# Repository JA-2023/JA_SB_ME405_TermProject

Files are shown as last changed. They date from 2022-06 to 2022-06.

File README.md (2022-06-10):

# Mechanical Design

For our robot we decided to go with a pantograph design which is a four arm system that is in the shape of a pentagram. This system is controlled by two stepper motors and connected at the end effector point. For the mechanical design we wanted to base it around the ability to be easily assembled and changed with little effort. To do this, we made a simple base that would hold the paper, electronics, and a raised platform on a hinge that the motors would sit on. For the arms, we wanted something light yet sturdy so we cut 4 arm linkages out of acrylic. For the joints of these arms, we wanted something to allow for fluid motion so we used standard bolts with nyloc nuts to allow for a snug but moveable connection. For the pen holder at the end of the arms, we used a brass sleeve bearing, which has a natural lubrication and a rubber grommet to make for a secure connection. To implement this design a 3D model was made using solidworks. From this 3D model made .DXF files and used to laser cut the arms from an acrylic sheet. The base was made from simple materials consisting of wood, screws, and metal hinges. For the half degree of degree of freedom a solenoid was connected to the motor platform and lifted via the hinges. There were some issues with this design which will be expanded upon in the problems/issues section.



                                           Figure 1:  3D model of pantograph robot

# Functionality

The Functionality of the Pantograph is intended to draw basic shapes, with two arms conjoined together and moving in a synchronized motion where at the intersection of the two arms, the pen is attached and drawing along the motion, if the pen in the instance is not suppose to draw anything , or go to the proper destination with no drawing, a solenoid is used (see Mechanical Design for more detail) to raise the platform , lifting the pen off the platform (see Figure 2 for a visual representation on how the Pantograph is suppose to work).  

 

                                          Figure 2: Pantograph Drawing a Square

# Kinematics

Forward Kinematics 

To calculate the Kinematics of the Pantograph, the design of the Pantograph is considered. In Figure 3 given four arms , four lengths are given : L1, L2, L3 , L4 and four angles : 𝛳<sub>1</sub>, 𝛳<sub>2</sub>, 𝛳<sub>3</sub>, 𝛳<sub>4</sub>.  The kinematics of the pantograph can be calculated. In Figure 3, C<sub>n</sub> and S<sub>n</sub> represent cos(𝛳<sub>n</sub>) and sin(𝛳<sub>n</sub>) respectively. Since we have two arms, the final destination, (x,y) is made up of two coordinates : (x<sub>1</sub>,y<sub>1</sub>), (x<sub>2</sub>, y<sub>2</sub>), with trigonometry , (x,y ) is calculated ( See Figure 3),    



                                          Figure 3: Kinematic model of system and Calculations

Inverse Kinematics 

The Inverse Kinematics is necessary , since in the Pantograph, it is taking the x-y coordinates as 

inputs , since the user wants to input coordinates and the robot needs to calculate the necessary angles to get the desired position. In order to calculate the inverse kinematics of the equation.The four kinematic equations are set up in a matrix as  f(𝛉) :

          

                                              Figure 4 - x, 𝛉, and  f(𝛉) set  as matrices.

Once set, the Jacobian matrix was found 



                                                   Figure 5 - Jacobian Matrix of f(𝛉)

Hence the coordinates , x is now a function of 𝛉 and since the Jacobian matrix is found, then it is possible to find the velocity kinematics  of the system  .



                                             Figure 6 - Velocity Kinematics of the Pantograph

Due to the level of complexity of the kinematics ,the velocity kinematics is utilized to help find the  Newton-Raphson algorithm,  a simple root-finding algorithm to iteratively solve the inverse kinematics, until the forward kinematics lands on a desired value for x. To do this first  g() needs to be solved for (see Figure 7), once solved,  g is solved for then (Figure 8).



                                              Figure 7 - Finding g()

                              

                                              Figure 8 - Finding g 

This new equation ( Figure 7) is selected so when g() is 0.  You can find the roots with the Newton Rhapson (Figure 9). The Newton-Raphson algorithm is a single-step iterative procedure for finding the roots of differential equations. In vector form and applied to this problem, The Newton-Raphson step would follow:

 

                                              Figure 9 - Newton-Raphson algorithm

where  n is the step number or number of iterations through the algorithm. The algorithm must stop when the value of g() is sufficiently close to zero by a threshold.

# Software Implementation and Design

## Driver Design



                                             Figure 10: Class diagram of the motor driver class

For the driver design the focus was on basic functionality that could be expanded upon if desired. The init class sets up the TMC2208 and TMC 4210 motor drivers to allow the motor to move. It sets up the necessary pins and SPI signals on the nucleo board as well as the clock, velocity, acceleration, movement mode, and so on. The set velocity, set acceleration, and acceleration calculations methods are used in the init class to set up the TMC drivers. The send and receive methods will take the datagram to be sent and then pull the chip select signal for a specific peripheral low and send the datagram through SPI. The set position method will take the target position datagram as a parameter. The target position is then passed into the function and bit masked,  so that the correct value is sent to the X position register of the TMC 4210. The read position method will read the data in the X actual register of the TMC 4210 and return the data read.

## Implementation of Kinematics

To solve the kinematics of the system for many different end effector positions a script was made that implements the kinematics described above. This script takes position values and puts them through three methods to output the desired motor angles. These methods are g which finds the difference between f(θ) and the destination, dg_dtheta which finds the jacobian, and NewtonRaphson which implements the iterative method described earlier. The Newton-Raphson function is passed a lambda function that allows the function to run continuously as if it was given theta values. Additionally a helper function, matmul, which multiplies a 4x1 matrix and a 4x4 matrix is used since there are limitations to micropython.

## Parsing Vector Images/interpolation

To allow the system to draw the desired shapes a vector drawing software was used and then that image was saved in a hpgl format. This format gives x and y coordinates along with a set of commands for controlling machines which are separated by semicolons (;). These commands include ones such as pen up (PU), select pen (SP), and pen down (PD). Pen down/up are the two main commands that were used for this system. These hpgl files were read as one large string and then were split at each semicolon to separate each command. Once that was done, each command was separated into a list which consisted of the command, a list of x positions, and a list of y positions.

Since our system is not perfect and the robot does not move smoothly from one point to the next, each point requires interpolation which is the process of adding more points between points to make smoother lines. Once all of the values are parsed they go through an interpolation script which adds the extra points and scales/off sets the positional values for this specific system. After that is done, all of the points go through the Newton-Raphson process to be changed to motor angles and written to a text file stored in the system flash to reduce the memory usage of the system. 

## Task Organization

To make this system work multiple elements had to work in tandem to make the robot work effectively. To do this a system called cotask was used which works as a way of scheduling tasks to make them seem to work simultaneously. This system works with 5 different tasks. The first and main task is read command. The read command task will read commands/motor angle values from a precompile text file and determine from the text which task it should execute next. If the command is pen up (PU), then the system will put a flag high indicating that the pen up task should begin. In the pen up task the system will turn on a solenoid, which in turn lifts the platform that the motors are on and then it will raise the read flag, so that the next command can be read. 

If the value read is pen down (PD), then it will raise a pen down flag and go to the pen down task. In this task, it will turn off the solenoid and then raise the flag to read another command. If the next command is a number then it will raise a flag to start the move arms task, and will then read the values for motor one and motor two and put them into shares. In the move arms task it will take the motor values from the shares and send the position to the motor driver to move the arms to the specified position. After the position is set the system will go to the update LCD task which will take those motor positions and send them to an LCD to give user feedback. Once this is done the read flag will be set high and the system will continue.



                                          Figure 11 - state diagram of task management

# Issues/Improvements to make

## Mechanical

Arm to motor connection:

One of the main issues encountered was the connection of the acrylic arms to the motor shaft. A good connection was not able to be made which resulted in the arm sometimes slipping and not moving correctly. To reduce this slipping, a wedge was used to make for a tighter connection. This was helpful but it is not intended to be a permanent solution. Due to this poor connection and the weight of the arms/hardware connected, the arms would sag down making them harder to move in a smooth and controlled fashion.

To fix this problem it would have been best to instead implement a gear reduction system and have the arms mesh with a gear to make a more secure connection. Also the material of the arms at the joints and end effector should be changed to a lighter material to reduce the drag. On top of this it would be better to implement a clamping mechanism to hold the pen instead of a wedging solution to allow for more fine tuning and flexibility.

Pen choice:

For this system we used a felt tip pen which would often bleed out onto the paper which did not make clean lines. The felt pen allowed for easy writing as it did not require much pressure but was not good since the plotter did not move very quickly.

A solution to this problem would be to use a smooth roller ball pen and slightly more pressure on the pen itself. This would result in cleaner but slightly lighter lines. The pen clamp holder solution mentioned above would work well with this type of pen since it would allow for the pressure to be tuned until a good balance between line thickness and drag was found.

Solenoid/lifting arms:

A large issue for this system was the weight of the motor platform and lifting it to create the half degree of freedom. The original solution was to use a solenoid to lift the platform holding the motors but due to the weight of the material used (wood) and the motors/arms the solenoid was not able to lift it reliably. The solenoid could hold the platform but it could not lift it. As a temporary fix a spring was used to reduce some of the downward force of the platform which helped to barely lift the pen but was not fully effective.

A potential solution to this issue would be to change the material used to make the platform and change the lifting mechanism. A scissor lift system using a dc motor would have been a much better choice as it would have allowed for precise control of the height of the platform; however, it would have made moving the platform up and down a little slower but the improved performance would outweigh this downside. As for the material, a 3d printed platform with a light material would allow for better strength and would have reduced the load on the solenoid. A potential problem with this solution however is that the material could have melted due to the heat of the motors. This potential problem could be mediated by using an insulating layer.

## Software

Memory issues:

One of the main issues with the software for this system was the limitations of the on board memory. Python uses a lot of memory whenever it makes a variable because of the built-in overhead for integers. On top of that list in python take a lot of space due to them automatically resizing when new elements are added. This would become an issue whenever an attempt to use high resolution DPI was made or if more interpolation points were added. To get around this issue, points generated were stored within a text file and then read when the arms were to be moved. This would improve the system slightly but memory issues would still occur even when storing values in the flash memory instead of RAM.

To improve upon this issue instead of processing and storing the data on the board I would process the vector image data on the main PC and then store the values found to a file and then store that file within the flash memory of the board. In addition, the memory issue could be avoided completely by storing the data on the computer and sending the values serially over UART to the microcontroller. This would slow down the system considerably but would completely circumvent the memory issues.  

Newton-Raphson:

Calculation of the motor angles using the Newton-Raphson method would sometimes result in an infinite loop because the error of the system would not get below the threshold value.

To fix this issue I would choose a different method to determine the angles of the system. This could result in a slightly less accurate system but would stop the system from getting stuck in an infinite loop. A possible solution would be to use the inverse kinematics of the system to find the angle values given an x and y position. A possible reference is this paper on another pantograph system <http://www.cim.mcgill.ca/~haptic/pub/GC-QW-VH-IROS-05.pdf>

# Conclusions

Overall this system in its current state gives lackluster results and due to the issue encountered did not produce the drawing desired. However, with the improvements mentioned above then the robot would most likely improve greatly over the results that we achieved. And could possibly result in very clean drawings.

# Pictures and Videos

<https://youtu.be/ho-xggbm21k>

Link 1: Video of the robot trying to draw a triangle

<https://youtu.be/eQrWwerRZpA>

Link 2: Video of LCD screen displaying motor position values



                                              Figure 12: Overhead view of Pantograph robot



                                  Figure 13: Motor driver board under platform connected to power supply and stepper motors
  

                          Figure 14: STM Nucleo board connected to stepper driver and bread board with circuitry for driving the solenoid.

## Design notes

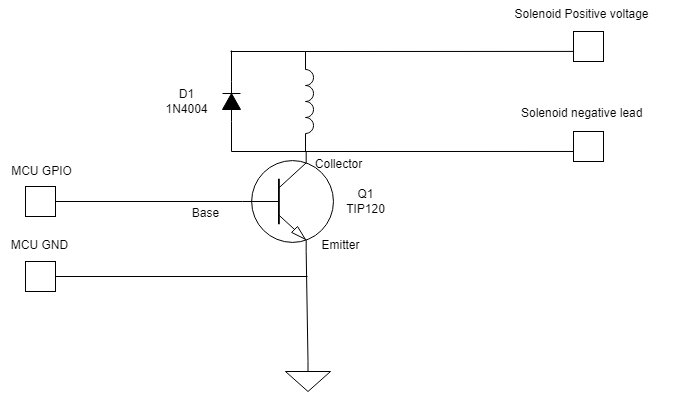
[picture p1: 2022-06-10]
Solenoid driver circuit.png

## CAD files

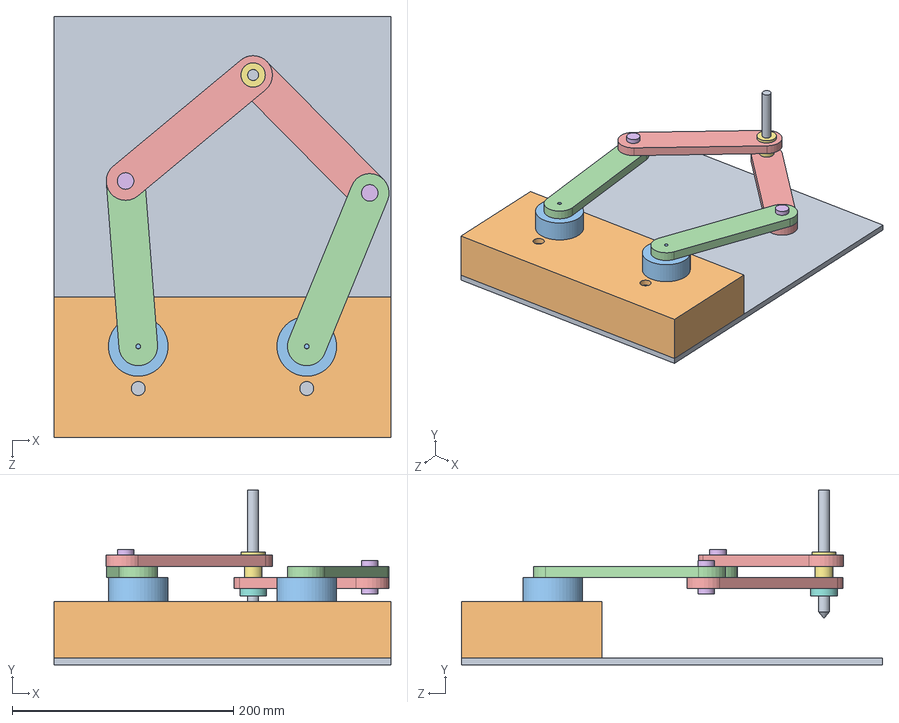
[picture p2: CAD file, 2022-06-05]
3dmodel/model_rev1.SLDASM
304.8 x 158.0 x 381.0 mm
base
motorBase
motor x 2
Arm_motor_joint x 2
Arm_pen_joint x 2
bearingPin x 2
sleeve_bearing
grommet
Pen

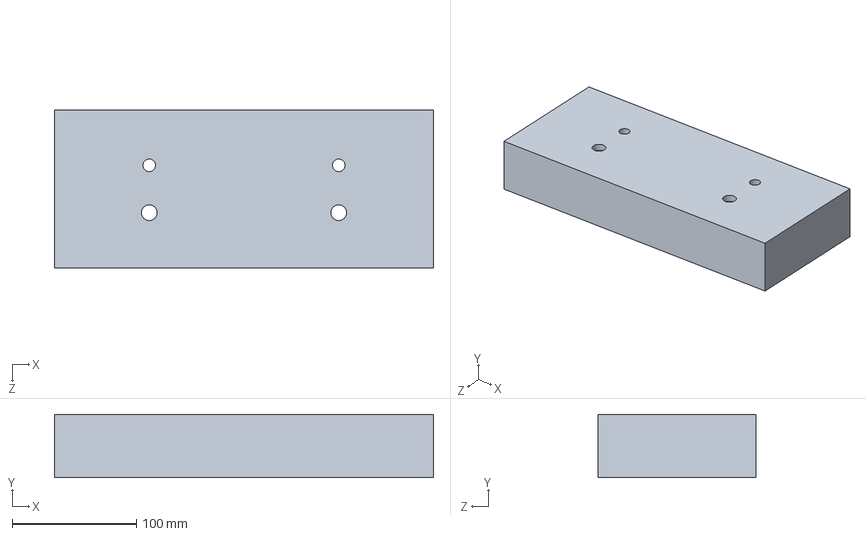
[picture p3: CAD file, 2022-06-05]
3dmodel/motorBase.SLDPRT
304.8 x 50.8 x 127.0 mm

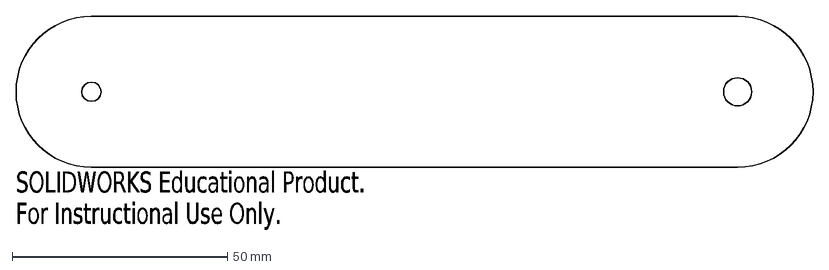
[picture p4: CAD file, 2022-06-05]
3dmodel/Arm_motor_joint_v1.DXF
SOLIDWORKS Educational Product.
For Instructional Use Only.

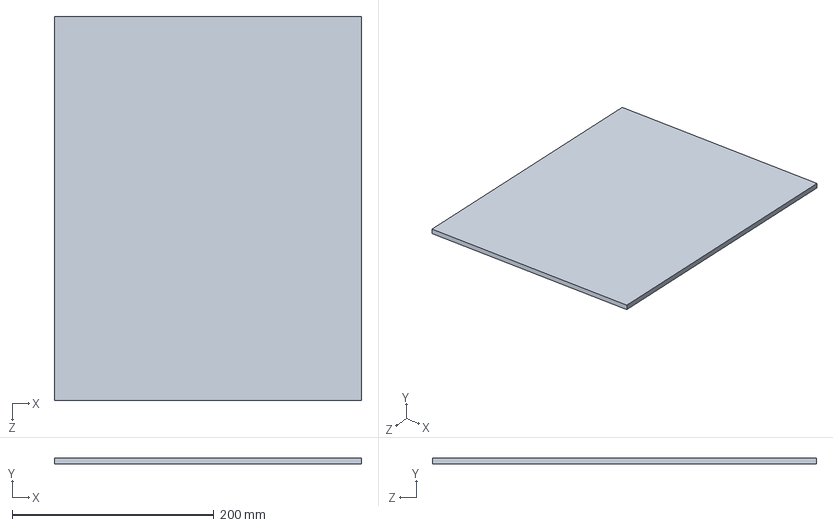
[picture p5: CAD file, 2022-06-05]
3dmodel/base.SLDPRT
304.8 x 6.35 x 381.0 mm

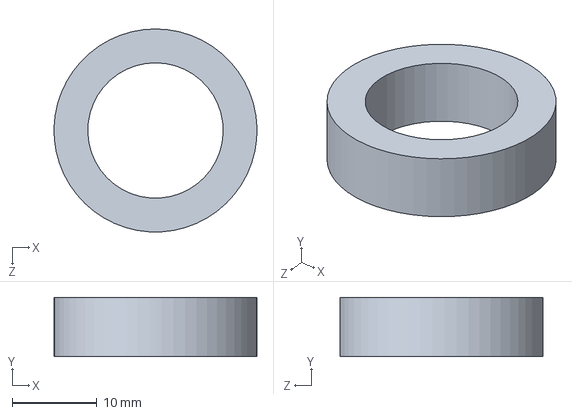
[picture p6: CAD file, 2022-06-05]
3dmodel/grommet.SLDPRT
24.0 x 7.00 x 24.0 mm

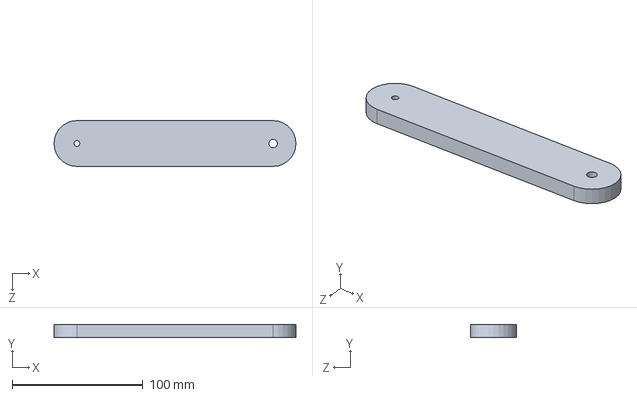
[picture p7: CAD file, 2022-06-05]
3dmodel/Arm_motor_joint.SLDPRT
185.0 x 10.0 x 35.0 mm

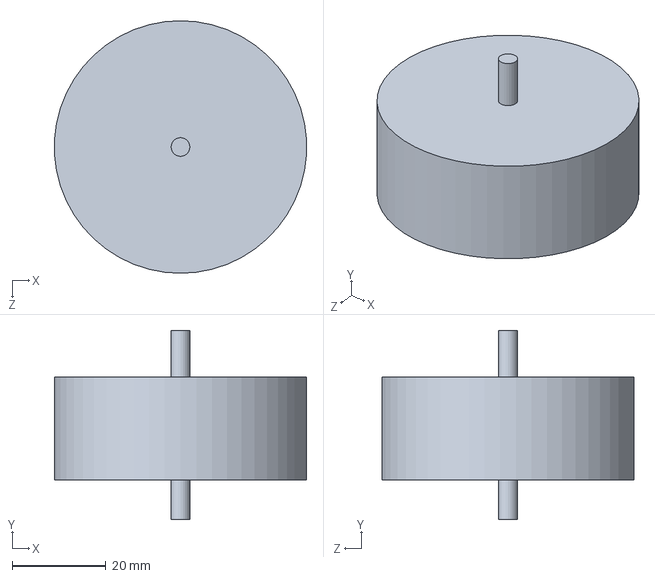
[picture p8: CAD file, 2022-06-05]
3dmodel/motor.SLDPRT
53.9 x 40.5 x 54.0 mm

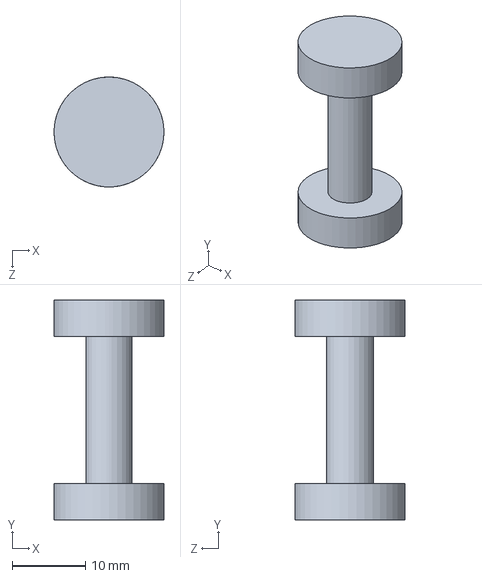
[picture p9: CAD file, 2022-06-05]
3dmodel/bearingPin.SLDPRT
15.0 x 30.0 x 15.0 mm

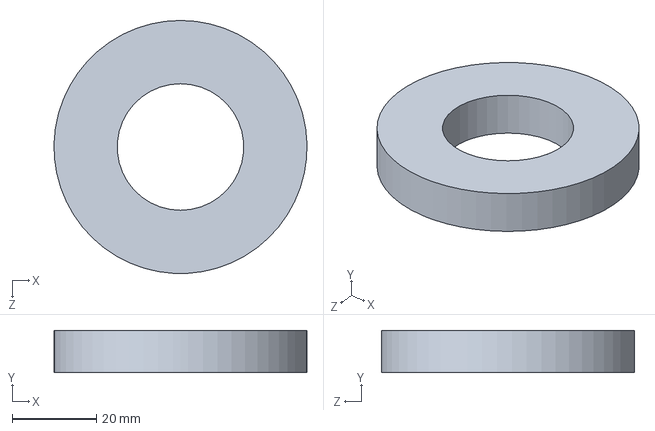
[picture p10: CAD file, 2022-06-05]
3dmodel/bearing.SLDPRT
60.0 x 10.0 x 60.0 mm

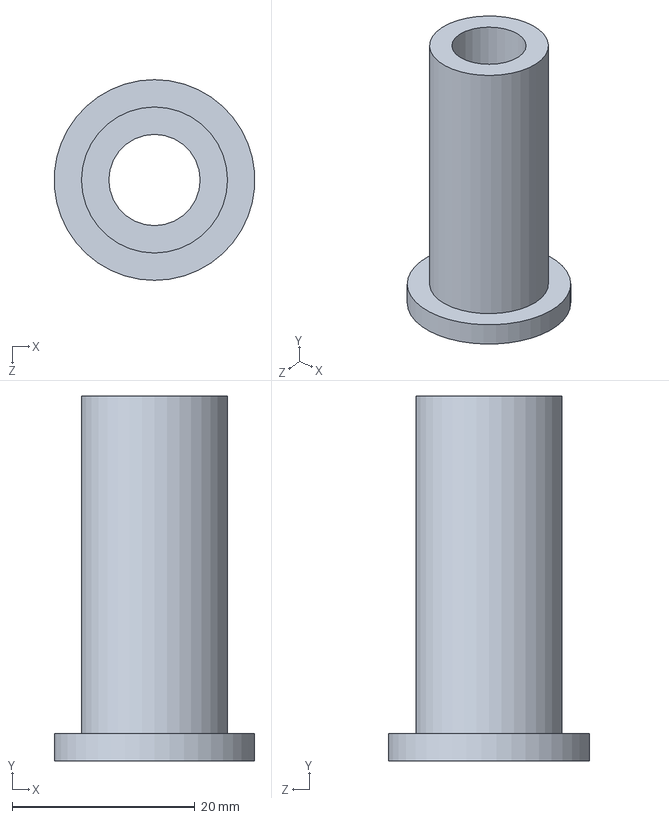
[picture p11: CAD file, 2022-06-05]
3dmodel/sleeve_bearing.SLDPRT
21.9 x 40.0 x 22.0 mm

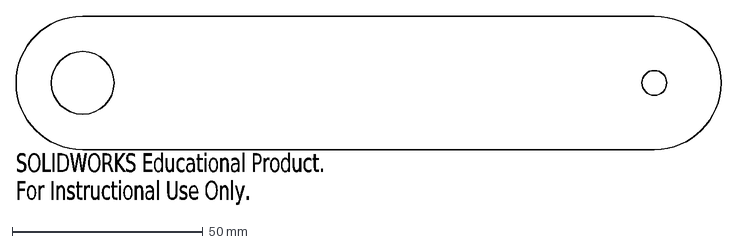
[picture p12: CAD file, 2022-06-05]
3dmodel/Arm_pen_joint_v1.DXF
SOLIDWORKS Educational Product.
For Instructional Use Only.

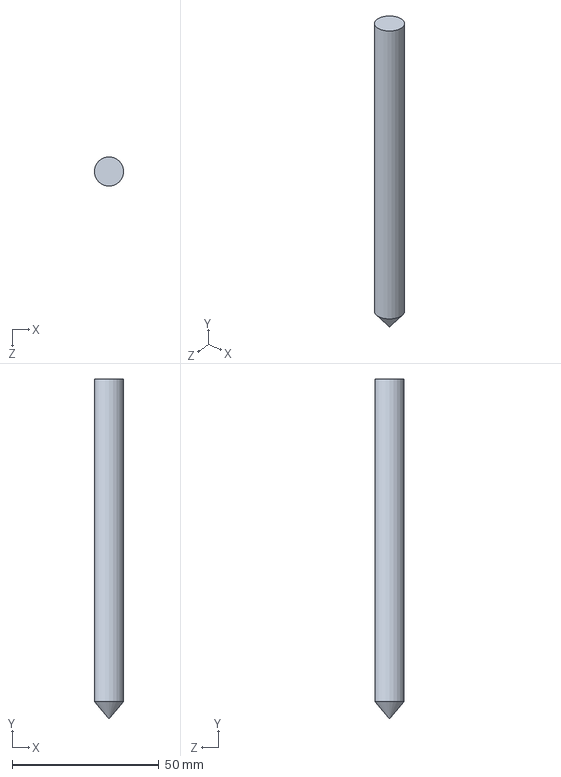
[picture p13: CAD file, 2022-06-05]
3dmodel/Pen.SLDPRT
10.0 x 116.0 x 10.0 mm

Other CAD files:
3dmodel/Arm_pen_joint.SLDPRT
3dmodel/Arm_motor_joint.DXF
3dmodel/Arm_pen_joint.DXF

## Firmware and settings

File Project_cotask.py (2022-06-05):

import micropython

from pyb import *

import gc
import cotask
import taskshare
import hpgl_reading
import project_driver as Driver
import machine
import lcd_api
import i2c_lcd
from machine import Pin, SoftI2C
from lcd_api import LcdApi
from i2c_lcd import I2cLcd
from time import sleep

#disable repl on uart
repl_uart(None)

#needed to output error messages
micropython.alloc_emergency_exception_buf(100)


def task_PenUp():
    while True:
        #check for pen up flag
        if PenUp_flag.get():
            print("in pen up")
            #turn on solenoid
            solenoid.high()
            #make pen up flag low
            PenUp_flag.put(0)
            #make read flag high to read next command
            Read_flag.put(1) 
        yield(0)

def task_PenDown():
    while True:
        #check for pen down flag
        if PenDown_flag.get():
            #turn off solenoid
            solenoid.low()
            #turn off pen down flag
            PenDown_flag.put(0)
            #make read flag high
            Read_flag.put(1)
        yield(0)
    
    
def task_MoveArms():
    while True:
        #check if move_arms flag is high
        if(Move_flag.get()):
            #read theta values from share and then set motor position
            TMC.set_position1(Motor1_angles.get())
            TMC.set_position2(Motor2_angles.get())
            
            #set move flag low
            Move_flag.put(0)

            #make LCD flag high
            LCD_flag.put(1)
        yield(0)


def task_UpdateLCD():
    
    while True:
        if LCD_flag.get():
            #moves cursor to second row (our lcd had issues)
            lcd.move_to(19,2)
            #put blank space at the end to clear 1s place on 3 digit numbers
            lcd.putstr(f" ")
            #move cursor to third row
            lcd.move_to(19,3)
            #put blank space at the end to clear 1s place on 3 digit numbers
            lcd.putstr(f" ")
            #move to beginning of second row and write out motor values
            lcd.move_to(0, 2)
            lcd.putstr(f"motor1 position: {Motor1_text.get()}")
            #move to beginning of third row and write out motor values
            lcd.move_to(0, 3)
            lcd.putstr(f"motor2 position: {Motor2_text.get()}")
            
            #set LCD flag low
            LCD_flag.put(0)

            #set flag to go to read task
            Read_flag.put(1)

        yield(0)

def task_ReadCommands():

    #open file to read motor angle values
    file = open('motor_values.txt','r')
    while True:
        
        if(Read_flag.get()):
            #read line of text from file
            txt1 = file.readline()
            #strip off newline character so it can be converted to number if needed
            txt1 = txt1.strip('\n')

            #will try to check the string read, if there is an index error then the end was reached
            #if the end was reached then stay in read task and close file
            try:
                #check if the text is a motor value
                if txt1[0].isdigit():
                    #convert value into an int and put it into a share
                    Motor1_angles.put(int(float(txt1)))
                    Motor1_text.put(int(float(txt1)))

                    #read next line from file to get second motor value
                    txt2 = file.readline()
                    txt2 = txt2.strip('\n')

                    #convert motor value into an int and put it into a share
                    Motor2_angles.put(int(float(txt2)))
                    Motor2_text.put(int(float(txt2)))

                    #set flag to go to the move task
                    Move_flag.put(1)
                else:
                    #check which command it is and go to the right task
                    if txt1 == 'PU':
                        #set flag high to go to pen up task
                        PenUp_flag.put(1)
                    if txt1 == 'PD':
                        #set flag high to go to pen down task
                        PenDown_flag.put(1)

                #set read flag low so it moves to next task 
                Read_flag.put(0)
            except:
                #idle in read command task
                Read_flag.put(1)
                file.close
        yield(0)

if __name__ == '__main__':
    
    #Initalize driver 
    TMC = Driver.Driver(7,7)

    #parse commands from hpgl file and put it into a text file
    hpgl_reading.parsing('drawing_1.hpgl')

    #make pin to turn solenoid on and off
    solenoid = Pin(Pin.cpu.C4, mode=Pin.OUT_PP, value = 0)
    
    #set up for I2C LCD
    I2C_ADDR = 0x27
    totalRows = 4
    totalColumns = 20
    SDA = Pin(Pin.cpu.B7)
    SCL = Pin(Pin.cpu.B6)
    i2c = SoftI2C(scl=SCL, sda=SDA, freq=5000) 
    lcd = I2cLcd(i2c, I2C_ADDR, totalRows, totalColumns)
    
    
    
    #set up shares
    LCD_flag = taskshare.Share('H', thread_protect = False, name = "LCD_share")
    PenUp_flag = taskshare.Share('H', thread_protect = False, name = "PU_share")
    PenDown_flag = taskshare.Share('H', thread_protect = False, name = "PD_share")
    Move_flag = taskshare.Share('H', thread_protect = False, name = "Move_share")
    Read_flag = taskshare.Share('H', thread_protect = False, name = "Read_share")
    command_counter = taskshare.Share('H', thread_protect = False, name = "Count_share")
    Motor1_angles = taskshare.Share('H', thread_protect = False, name = "angle1_share")
    Motor2_angles = taskshare.Share('H', thread_protect = False, name = "angle2_share")
    Motor1_text = taskshare.Share('H', thread_protect = False, name = "text1_share")
    Motor2_text = taskshare.Share('H', thread_protect = False, name = "text2_share")
 
    #set up tasks
    PD_task = cotask.Task(task_PenDown, name = 'button_task', priority = 2,
                              period = 150, profile = True, trace = False)
    
    PU_task = cotask.Task(task_PenUp, name = 'button_task', priority = 2,
                              period = 150, profile = True, trace = False)

    Read_task = cotask.Task(task_ReadCommands, name = 'button_task', priority = 3,
                              period = 150, profile = True, trace = False)

    LCD_task = cotask.Task(task_UpdateLCD, name = 'button_task', priority = 1,
                              period = 100, profile = True, trace = False)

    Move_task = cotask.Task(task_MoveArms, name = 'button_task', priority = 3,
                              period = 100, profile = True, trace = False)                          
                          
    
    #add task to list
    cotask.task_list.append(PD_task)
    cotask.task_list.append(PU_task)
    cotask.task_list.append(Read_task)
    cotask.task_list.append(LCD_task)
    cotask.task_list.append(Move_task)
    
    gc.collect()
    
    #start in read task
    Read_flag.put(1)

    while True:
        cotask.task_list.pri_sched()

    




    

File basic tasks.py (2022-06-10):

"""!
@file basic_tasks.py
    This file contains a demonstration program that runs some tasks, an
    inter-task shared variable, and a queue. The tasks don't really @b do
    anything; the example just shows how these elements are created and run.

@author JR Ridgely
@date   2021-Dec-15 JRR Created from the remains of previous example
@copyright (c) 2015-2021 by JR Ridgely and released under the GNU
    Public License, Version 2. 
"""

import gc
import pyb
import cotask
import task_share


def task1_fun ():
    """!
    Task which puts things into a share and a queue.
    """
    counter = 0
    while True:
        share0.put (counter)
        q0.put (counter)
        counter += 1

        yield (0)


def task2_fun ():
    """!
    Task which takes things out of a queue and share to display.
    """
    while True:
        # Show everything currently in the queue and the value in the share
        print ("Share: {:}, Queue: ".format (share0.get ()), end='');
        while q0.any ():
            print ("{:} ".format (q0.get ()), end='')
        print ('')

        yield (0)


# This code creates a share, a queue, and two tasks, then starts the tasks. The
# tasks run until somebody presses ENTER, at which time the scheduler stops and
# printouts show diagnostic information about the tasks, share, and queue.
if __name__ == "__main__":
    print ('\033[2JTesting ME405 stuff in cotask.py and task_share.py\r\n'
           'Press ENTER to stop and show diagnostics.')

    # Create a share and a queue to test function and diagnostic printouts
    share0 = task_share.Share ('h', thread_protect = False, name = "Share 0")
    q0 = task_share.Queue ('L', 16, thread_protect = False, overwrite = False,
                           name = "Queue 0")

    # Create the tasks. If trace is enabled for any task, memory will be
    # allocated for state transition tracing, and the application will run out
    # of memory after a while and quit. Therefore, use tracing only for 
    # debugging and set trace to False when it's not needed
    task1 = cotask.Task (task1_fun, name = 'Task_1', priority = 1, 
                         period = 400, profile = True, trace = False)
    task2 = cotask.Task (task2_fun, name = 'Task_2', priority = 2, 
                         period = 1500, profile = True, trace = False)

    cotask.task_list.append (task1)
    cotask.task_list.append (task2)

    # Run the memory garbage collector to ensure memory is as defragmented as
    # possible before the real-time scheduler is started
    gc.collect ()

    # Run the scheduler with the chosen scheduling algorithm. Quit if any 
    # character is received through the serial port
    vcp = pyb.USB_VCP ()
    while not vcp.any ():
        cotask.task_list.pri_sched ()

    # Empty the comm port buffer of the character(s) just pressed
    vcp.read ()

    # Print a table of task data and a table of shared information data
    print ('\n' + str (cotask.task_list))
    print (task_share.show_all ())
    print (task1.get_trace ())
    print ('\r\n')

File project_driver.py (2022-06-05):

import micropython

from pyb import *


#needed to output error messages
micropython.alloc_emergency_exception_buf(100)

#init/set up
class Driver:
    
    
    def __init__(self, PULSE_DIV, RAMP_DIV):
        #set up pins
        #CS1 = PC2
        self.CS1 = Pin(Pin.cpu.C2, mode=Pin.OUT_PP, value = 1)
        
        #CS2 = PC0
        self.CS2 = Pin(Pin.cpu.C0, mode=Pin.OUT_PP, value = 1)

        #TMC2208 ENN1 = PC3
        TMC_ENN1 = Pin(Pin.cpu.C3, mode=Pin.OUT_PP, value = 1)

        #TMC2208 ENN2 = PB0
        TMC_ENN2 = Pin(Pin.cpu.B0, mode=Pin.OUT_PP, value = 1)

        #CLK = PB3
        CLK = Pin(Pin.cpu.B3, mode=Pin.OUT_PP, value = 1)
        
        #set up SPI
        #SPI(2),(NSS, SCK, MISO, MOSI) = (PB12, PB13, PB14, PB15)
        self.spi = SPI(2, SPI.CONTROLLER, baudrate = 2000000, polarity = 1, phase = 1)
        

        #set up timer/timer channel
        clk_timer = Timer(2, period = 3, prescaler = 0)
        CLK = clk_timer.channel(2, pin = CLK, mode = Timer.PWM, pulse_width = 2)
        
        #enable TMC2208_1
        TMC_ENN1.low()

        #enable TMC2208_2
        TMC_ENN2.low()
        
        #enable TMC4210
        #set en_sd bit in config reg
        TMC4210_data = bytearray([0X68,0x00 ,0x00,0x20])
        
        
        #TMC1 en_sd = 1
        self.send_recv1(TMC4210_data)

        #TMC2 en_sd = 1
        self.send_recv2(TMC4210_data)

        #set veloctiy values for both drivers
        self.set_velocity(0x7FF, 0x00F)
        
        #set clock pre-dividers, PULSE_DIV, RAMP_DIV
        PULE_RMP_BITS = (PULSE_DIV << 4) + RAMP_DIV #this should work
        DIV_data = bytearray([0x18,0x00,PULE_RMP_BITS,0x00])
        
        self.send_recv1(DIV_data)
        self.send_recv2(DIV_data)
        
        #set A_max with pmul and pdiv
        self.set_acceleration(3000, PULSE_DIV, RAMP_DIV) 
        
        
        #set ramp mode
        #set bits 1-0 to 00 at address 0001010 rest are 0s
        RMP_data = bytearray([0x14,0x00,0x00,0x00])

        self.send_recv1(RMP_data)
        self.send_recv2(RMP_data)
        
        
        #set mot1r to 1
        motor_data = bytearray([0x7E,0x20,0x00,0x00])
        
        self.send_recv1(motor_data)
        self.send_recv2(motor_data)
        
        #can set target positions after this is done
        
    #set veloctiy
    def set_velocity(self, V_MAX, V_MIN):
        
        
        #set velocity parameters V_MIN and V_MAX
        V_MIN_upper = (0x700 & V_MIN) >> 8 #gets the last 3 bits of V_MIN
        V_MIN_lower = (0x0FF & V_MIN) #gets the first byte
        VMIN_data = bytearray([0x04, 0x00, V_MIN_upper, V_MIN_lower])
        
        V_MAX_upper = (0x700 & V_MAX) >> 8 #gets last 3 data bits and shifts them by a byte
        V_MAX_lower = (0x0FF & V_MAX) #gets the first byte
        VMAX_data = bytearray([0x06, 0x00, V_MAX_upper, V_MAX_lower])
        
        #send the data to TMC1
        self.send_recv1(VMIN_data)
        self.send_recv1(VMAX_data)

        #send the data to TMC2
        self.send_recv2(VMIN_data)
        self.send_recv2(VMAX_data)

        
    #set acceleration
    def set_acceleration(self, A_MAX, PULSE_DIV, RAMP_DIV):

        #send A_MAX to address 00001100 data in bits 0-10
        A_MAX_upper = (0x0700 & A_MAX) >> 8
        A_MAX_lower = (0x00FF & A_MAX)
        A_MAX_data = bytearray([0x0C, 0x00, A_MAX_upper, A_MAX_lower])

        #send amax to TMC1
        self.send_recv1(A_MAX_data)

        #send amax to TMC2
        self.send_recv2(A_MAX_data)

        #calculate PMUL/PDIV
        calc_vals = self.accel_calc(A_MAX, PULSE_DIV, RAMP_DIV)

        pmul = 0xFF & int(calc_vals[0])
        pdiv = 0x0F & calc_vals[1]

        Pmul_div_data = bytearray([0x12, 0x00, pmul, pdiv])

        #send data to TMC1
        self.send_recv1(Pmul_div_data)

        #send data to TMC2
        self.send_recv2(Pmul_div_data)
        


    #acceleration calc
    def accel_calc(self, A_MAX, PULSE_DIV, RAMP_DIV):

        p = A_MAX / (128.0 * pow(2, (RAMP_DIV - PULSE_DIV)))
        for pmul in range(128,255):
            for p_num in range(3,16):
                
                pdiv = 2**p_num
                p_val = pmul/pdiv
                q = p_val/p
                
                if((0.95 <= q) and (q <= 1.0)):
                    PMUL = pmul
                    PDIV = pdiv
                    break
        
        pmul = int(pmul)
        return pmul, pdiv
        
    #set target position of TMC1
    def set_position1(self, X_TARGET):
        
        #Mask data and shift to set byte array data
        X_byte_1 = (X_TARGET & 0xFF0000) >> 16
        X_byte_2 = (X_TARGET & 0x00FF00) >> 8
        X_byte_3 = (X_TARGET & 0x0000FF)

        X_data = bytearray([0x00,X_byte_1,X_byte_2,X_byte_3])
        self.send_recv1(X_data)
    
    #set target position of TMC2
    def set_position2(self, X_TARGET):
        
        #Mask data and shift to set byte array data
        X_byte_1 = (X_TARGET & 0xFF0000) >> 16
        X_byte_2 = (X_TARGET & 0x00FF00) >> 8
        X_byte_3 = (X_TARGET & 0x0000FF)

        X_data = bytearray([0x00,X_byte_1,X_byte_2,X_byte_3])
        self.send_recv2(X_data)
        
    #get position
    def read_position1(self):
        X_read = bytearray([0x03, 0x00, 0x00, 0x00])
        data_read = bytearray(4)

        #send/recieve data
        data_read = self.send_recv1(X_read) #sends the address and stuff recieved should be the X data

        return data_read

    #get position
    def read_position2(self):
        X_read = bytearray([0x03, 0x00, 0x00, 0x00])
        data_read = bytearray(4)

        #send/recieve data
        data_read = self.send_recv2(X_read) #sends the address and stuff recieved should be the X data

        return data_read

        
    def send_recv1(self, datagram):
        #buffer to hold return values
        rxbuf = bytearray(4)
        #pull CS low to start transmission
        self.CS1.low()
        #send bytes
        self.spi.send_recv(datagram, rxbuf) #hold bytes recieved in variable
        #set chip select high to stop transmission
        self.CS1.high()
        #return data
        return rxbuf

    def send_recv2(self, datagram):
        #buffer to hold return values
        rxbuf = bytearray(4)
        #pull CS low to start transmission
        self.CS2.low()
        #send bytes
        self.spi.send_recv(datagram, rxbuf) #hold bytes recieved in variable
        #set chip select high to stop transmission
        self.CS2.high()
        #return data
        return rxbuf

    
